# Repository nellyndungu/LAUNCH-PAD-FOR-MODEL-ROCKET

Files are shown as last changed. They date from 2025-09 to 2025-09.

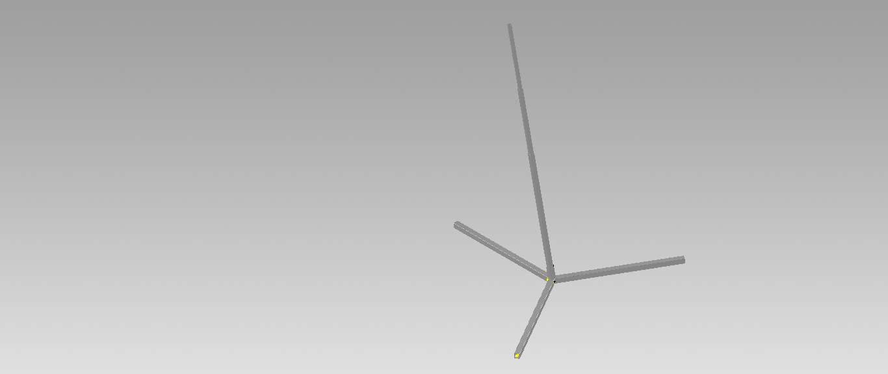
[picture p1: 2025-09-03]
LP001/LP.png

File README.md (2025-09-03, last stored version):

# LAUNCHPAD DESIGN
## DESIGN CONSIDERATION
1. Structural integrity.
The launchpad should withstand the forces/ thrust generated by the rocket during liftoff.
- Strong and rigid structural members – consider the material and the cross-sections and the suitable length.
- Stable base – consider the most stable base shape whether the square or triangle base.
- Assembly technique – consider single launch rail support or telescopic joining of the rail support.
- Fastening – Use of bolts. Consider the appropriate bolts to use.
2. Rocket alignment.
Use Open Rocket to find the vertical angle offset for optimum stability during lift off. Practical method of loading the rocket onto the launchpad.
- Easy rocket loading – release system for loading of rocket onto the launchpad.
3. Rocket launchpad height.
The launch rail required length of 5m. This requires launch support of 4m and an overhang of 1m.
4. Portability – Easy setup and portability.
- Telescopic assembly for launch rail support.
- Detachable base.
5. Fabrication.
The launchpad design should allow for fabrication using standard materials and locally available fabrication methods.
## Expected loading
1. Thrust generated by the rocket and weight of the rocket (Actual load)
2. Horizontal component of actual load – acts on the rail support beam.
## Design calculations
The mean thrust of the motor is 3kN. Using a safety factor of 2:
The design load is given by:
$ L_d = SF \times L_a $
where $L_d$ is design load, $SF$ is safety factor and $L_a$ is the actual load resulting to design load of 6 kN.
The horizontal component of the design load is given by:
$$ F_h = L_d \times sin \alpha $$
where $F_h$ is horizontal component of design load and \alpha is rocket tilt angle of 5° resulting to 523 N. The launch rail assumes a cantilever fixed at different point and made of hollow square tubes. The design load shall be used to calculate the base dimensions and base member sizing. The horizontal component force shall be used to size the rail support beams and their cross-section. The rail support is a cantilever beam with point load and fixed at base of the launchpad.

Taking:
- Length of beam (L) = 4 m = 4000 mm
- Point load (𝐹ℎ) = 523 N
- Material: Mild steel Yield strength (𝜎𝑦) = 250 MPa, E = 200 GPa
- Hollow square section:
$$ I = \frac{B^4 - (B - 2t) ^4}{12} $$
where $I$ is moment of inertia $B$ is the side of square tube in mm and $t$ is thickness of tube in mm.

    1. Maximum bending moment ($𝑀_{𝑚𝑎𝑥}$):
    $$ M_{max} = F_h \times L$$
    resulting to 2,092,000 Nmm
  2. Section modulus (S)
    $$ \sigma_{max} = \frac{|M_{max}| \cdot C}{I} \le \sigma_y $$
    Since:
       $$ S = \frac{I}{C} $$
           then
        $$ \sigma_{max} = \frac{|M_{max}|}{S} $$:
        $$ S = \frac{|M_{max}|}{\sigma_{max}} $$
  resulting to 8368 $mm^3$
  3. Cross-section dimensions $(B)$
  $$ I = \frac{B^4 - (B - 2t)^4}{12} $$
  Taking thickness of 3 mm:
  $$ S = \frac{B^4 - (B - 2t)^4}{12} $$
  resulting to 8368 $mm^3$
Expanding the equation using binomial expansion and solving for B as 50mm.
4. Check for maximum deflection.
Maximum deflection is given by:
$$ \delta = \frac{FL^3}{3EI} $$
The  moment of inertia I for the 70mm hollow square cross-section is given as:
$$ I = \frac{B^4 - (B - 2t)^4}{12} $$ resulting to 208,492 $mm^4$
The maximum deflection was found to be 268 mm. This deflection is huge and exceeds the maximum allowable deflection.

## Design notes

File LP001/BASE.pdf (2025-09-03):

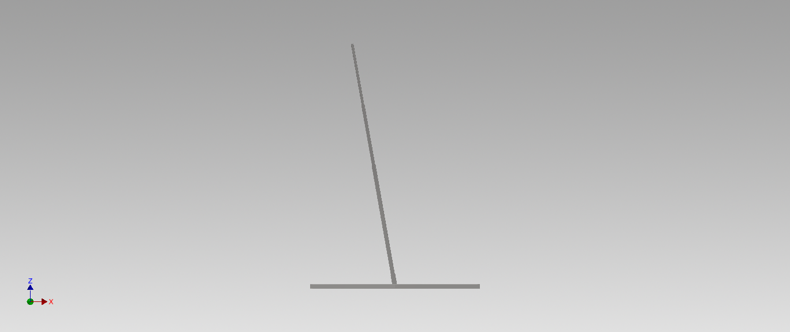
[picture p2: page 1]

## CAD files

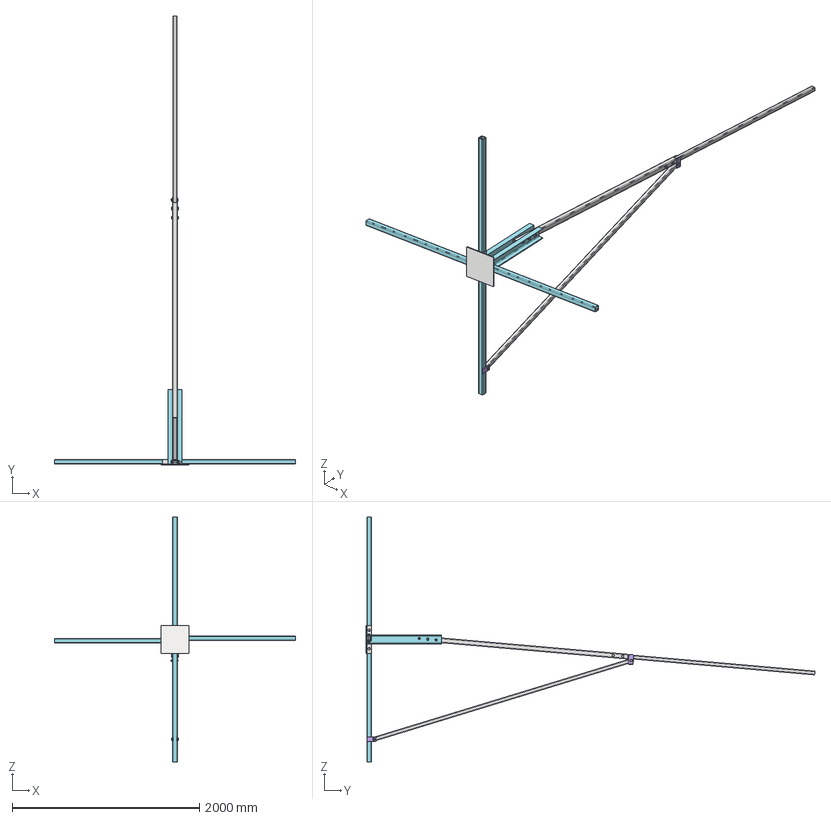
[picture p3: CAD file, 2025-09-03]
LP003/LPTL_ASSEMBLY.stp
2571.8 x 4791.2 x 2610.0 mm
BASE PLATE
U_SECTION x 2
Skeleton 1744276058427 x 2
ISO 657_11 CH 100 x 10 1744276061340
LEG_ATTACHMENT1
LEG_ATTACHMENT1_1
LEG_ATTACHMENT1_4 x 2
LEG x 4
Skeleton 1744274640470 x 4
ISO 12633-2 50x50x5 1744274642458 x 2
ANSI B18.2.3.5M - M16 x 2 x 80 x 5
ANSI B 18.2.4.1 M - M16 x 2 x 11
ISO 657_11 CH 100 x 10 1744276061340_1
LEG_ATTACHMENT1_2
LEG_ATTACHMENT1_3
ISO 12633-2 50x50x5 1744274642458_1
ISO 12633-2 50x50x5 1744274642458_2
ANSI B18.2.3.5M - M16 x 2 x 75 x 2
TL_FRAME x 2
Skeleton 1744350249536
ISO 10799-2 40x40x4 1744350251503
Skeleton 1744350148993
ISO 10799-2 50x50x4 1744350151616
ANSI B18.2.3.5M - M16 x 2 x 65 x 4
SUPPORT ATTACHMENT
SUPPORT ATTACHMENT_1
SUPPORT ATTACHMENT_2
SUPPORT ATTACHMENT_3
ENFORCEMENT_1
Skeleton 1744705197973
ISO 10799-2 40x40x4 1744708078713

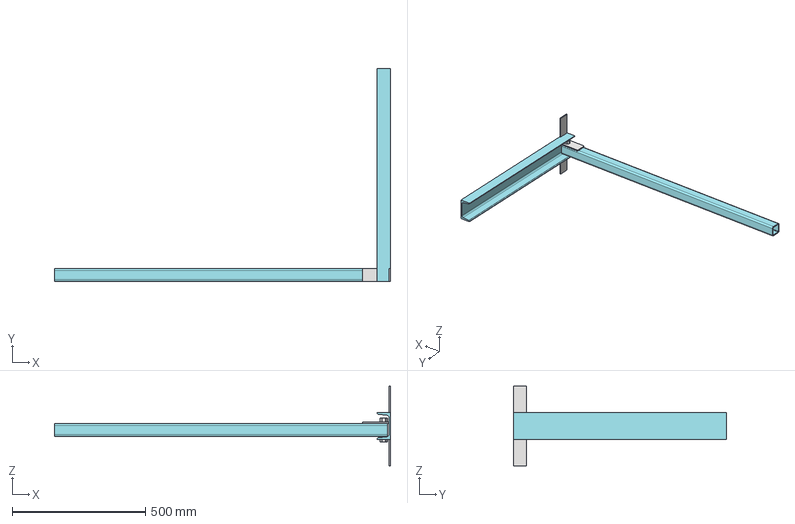
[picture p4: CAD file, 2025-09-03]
LP003/STEP_FILES/CHANNEL_LEG ASSEMBLY.stp
1260.9 x 800.0 x 300.0 mm
U_SECTION
Skeleton 1744276058427
ISO 657_11 CH 100 x 10 1744276061340
LEG_ATTACHMENT1 x 2
LEG_ATTACHMENT1_1
LEG
Skeleton 1744274640470
ISO 12633-2 50x50x5 1744274642458
ANSI B18.2.3.5M - M16 x 2 x 80
ANSI B 18.2.4.1 M - M16 x 2

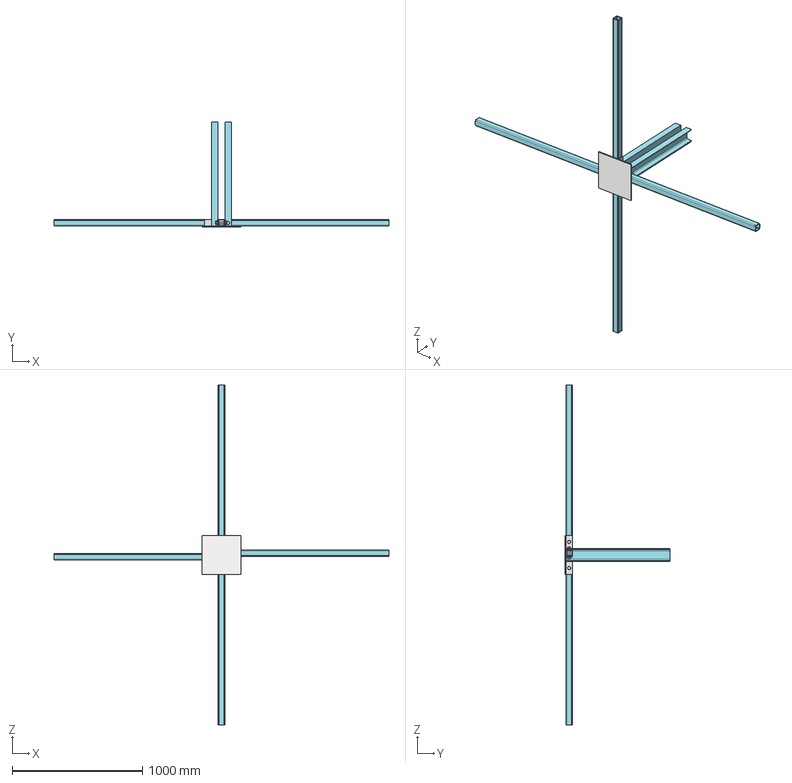
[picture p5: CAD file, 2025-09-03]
LP003/STEP_FILES/BASE_ASSEMBLY.stp
2571.8 x 808.0 x 2610.0 mm
BASE PLATE
U_SECTION x 2
Skeleton 1744276058427 x 2
ISO 657_11 CH 100 x 10 1744276061340 x 2
LEG_ATTACHMENT1
LEG_ATTACHMENT1_1
LEG_ATTACHMENT1_4 x 2
LEG x 4
Skeleton 1744274640470 x 4
ISO 12633-2 50x50x5 1744274642458 x 2
ANSI B18.2.3.5M - M16 x 2 x 80 x 2
ANSI B 18.2.4.1 M - M16 x 2 x 4
LEG_ATTACHMENT1_2
LEG_ATTACHMENT1_3
ISO 12633-2 50x50x5 1744274642458_1
ISO 12633-2 50x50x5 1744274642458_2
ANSI B18.2.3.5M - M16 x 2 x 75 x 2

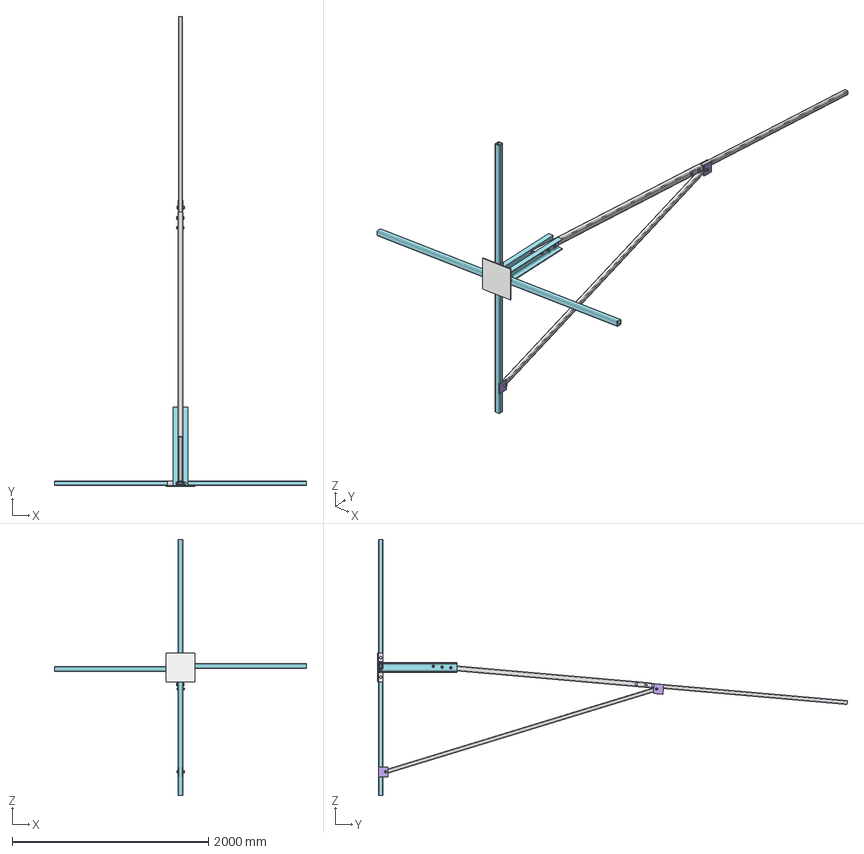
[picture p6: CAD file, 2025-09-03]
LP003/STEP_FILES/LPTL_ASSEMBLY WITH SUPPORT.stp
2571.8 x 4791.2 x 2610.0 mm
BASE PLATE
U_SECTION x 2
Skeleton 1744276058427 x 2
ISO 657_11 CH 100 x 10 1744276061340
LEG_ATTACHMENT1
LEG_ATTACHMENT1_1
LEG_ATTACHMENT1_4 x 2
LEG x 4
Skeleton 1744274640470 x 4
ISO 12633-2 50x50x5 1744274642458 x 2
ANSI B18.2.3.5M - M16 x 2 x 80 x 5
ANSI B 18.2.4.1 M - M16 x 2 x 11
ISO 657_11 CH 100 x 10 1744276061340_1
LEG_ATTACHMENT1_2
LEG_ATTACHMENT1_3
ISO 12633-2 50x50x5 1744274642458_1
ISO 12633-2 50x50x5 1744274642458_2
ANSI B18.2.3.5M - M16 x 2 x 75 x 2
TL_FRAME x 2
Skeleton 1744350249536
ISO 10799-2 40x40x4 1744350251503
Skeleton 1744350148993
ISO 10799-2 50x50x4 1744350151616
ANSI B18.2.3.5M - M16 x 2 x 65 x 4
SUPPORT ATTACHMENT
SUPPORT ATTACHMENT_1
ENFORCEMENT_1
Skeleton 1744705197973
ISO 10799-2 40x40x4 1744708078713
SUPPORT ATTACHMENT_2
SUPPORT ATTACHMENT_3

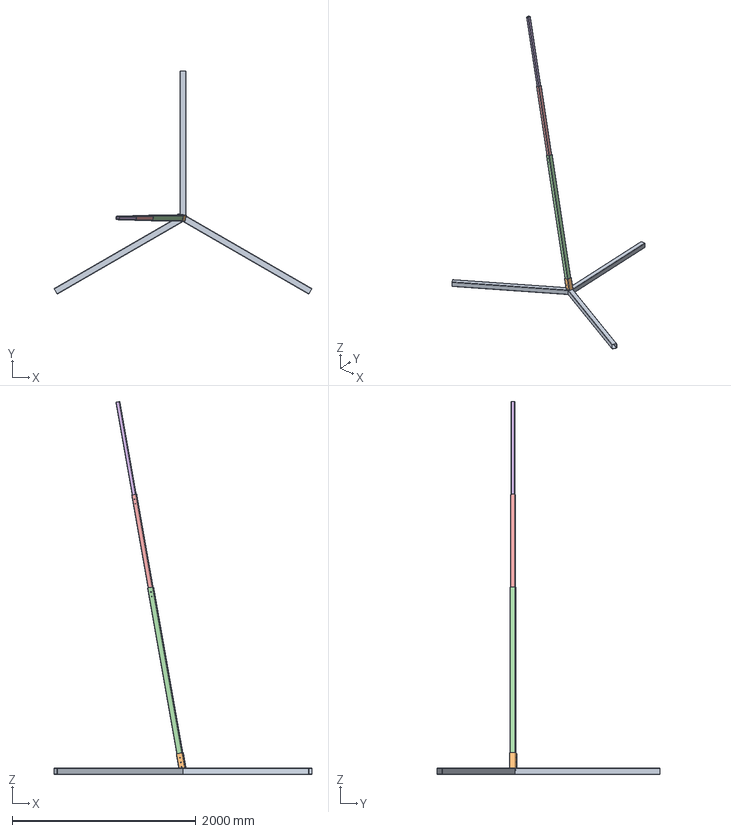
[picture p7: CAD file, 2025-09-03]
LP001/LAUNCHPAD.stp
2806.3 x 2430.3 x 4058.9 mm
BASE_1
Skeleton 1743054956772
ISO 10799-2 - 70x70x3 - 1600
ISO 10799-2 - 70x70x3 - 1600_1
ISO 10799-2 - 70x70x3 - 1600_2
ISO 10799-2 - 70x70x3 - 200
LP_01
Skeleton 1743052582824
ISO 10799-2 - 60x60x3 - 2000
LP_02 x 2
Skeleton 1743058174036
ISO 10799-2 - 50x50x3 - 1150
Skeleton 1743060041599
ISO 10799-2 - 40x40x3 - 1150

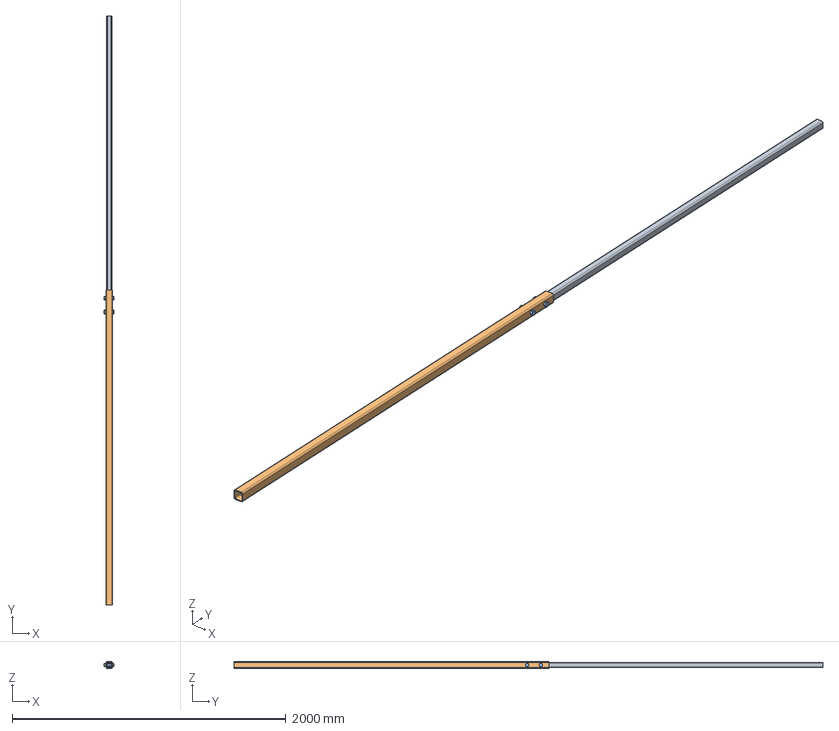
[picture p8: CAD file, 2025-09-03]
LP003/STEP_FILES/TL_50_40.stp
75.8 x 4300.0 x 50.0 mm
TL_FRAME x 2
Skeleton 1744350249536
ISO 10799-2 40x40x4 1744350251503
Skeleton 1744350148993
ISO 10799-2 50x50x4 1744350151616
ANSI B18.2.3.5M - M16 x 2 x 65 x 2
ANSI B 18.2.4.1 M - M16 x 2 x 2

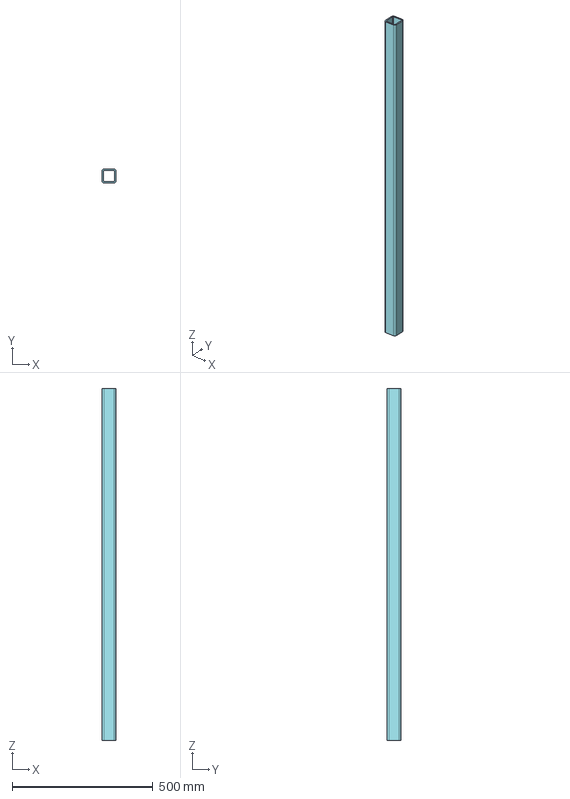
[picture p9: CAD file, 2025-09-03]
LP003/STEP_FILES/LEG_50.stp
50.0 x 50.0 x 1250.0 mm
LEG
Skeleton 1744274640470
ISO 12633-2 50x50x5 1744274642458

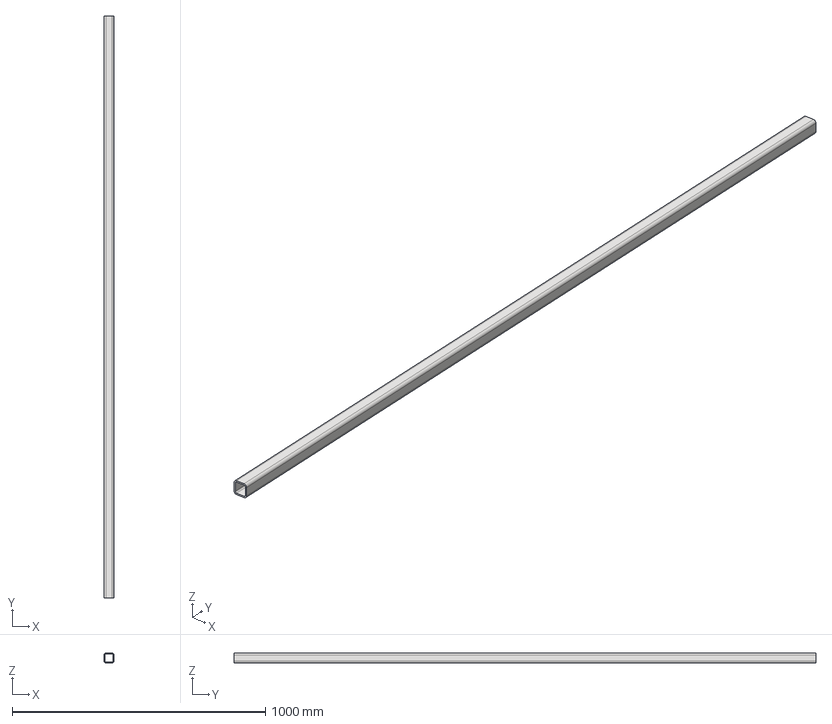
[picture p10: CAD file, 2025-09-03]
LP003/STEP_FILES/TL_40.stp
40.0 x 2300.0 x 40.0 mm
TL_FRAME
Skeleton 1744350249536
ISO 10799-2 40x40x4 1744350251503

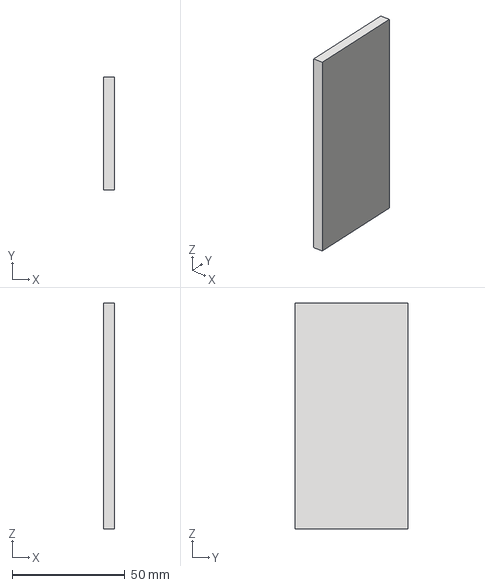
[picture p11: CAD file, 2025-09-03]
LP003/STEP_FILES/LEG_ATTACHMENT1.stp
5.00 x 50.0 x 100.0 mm

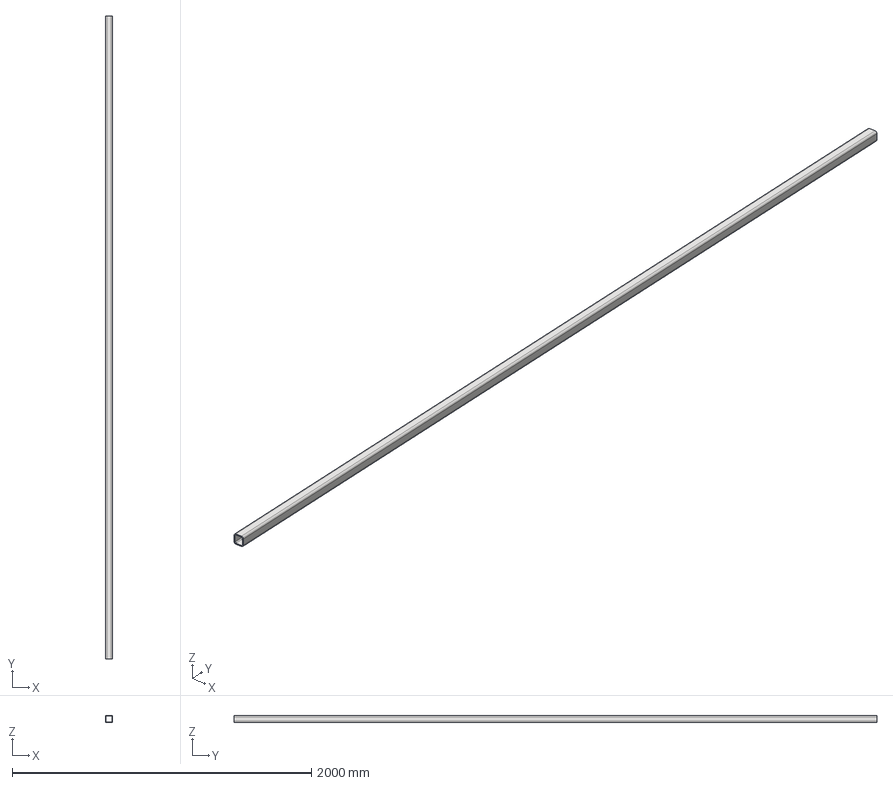
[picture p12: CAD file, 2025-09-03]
LP003/STEP_FILES/RAIL_SUPPORT_50.stp
50.0 x 4300.0 x 50.0 mm
RAIL_SUPPORT
Skeleton 1744280627170
ISO 10799-2 50x50x5 1744280629508

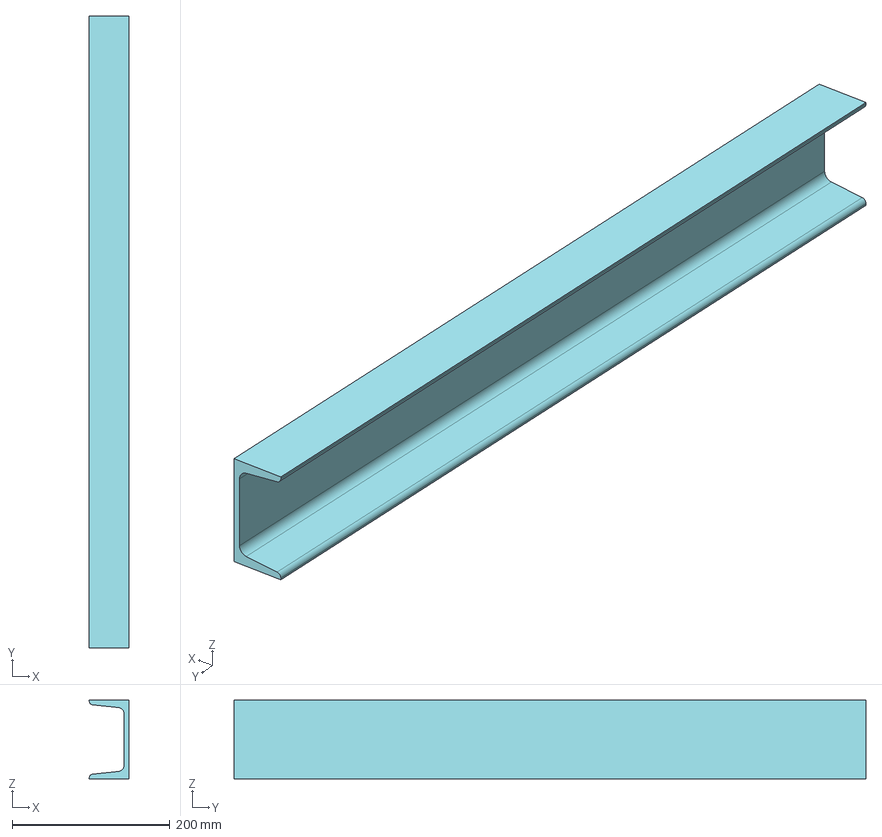
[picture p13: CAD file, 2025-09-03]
LP003/STEP_FILES/U_SECTION_50.stp
50.0 x 800.0 x 100.0 mm
U_SECTION
Skeleton 1744276058427
ISO 657_11 CH 100 x 10 1744276061340

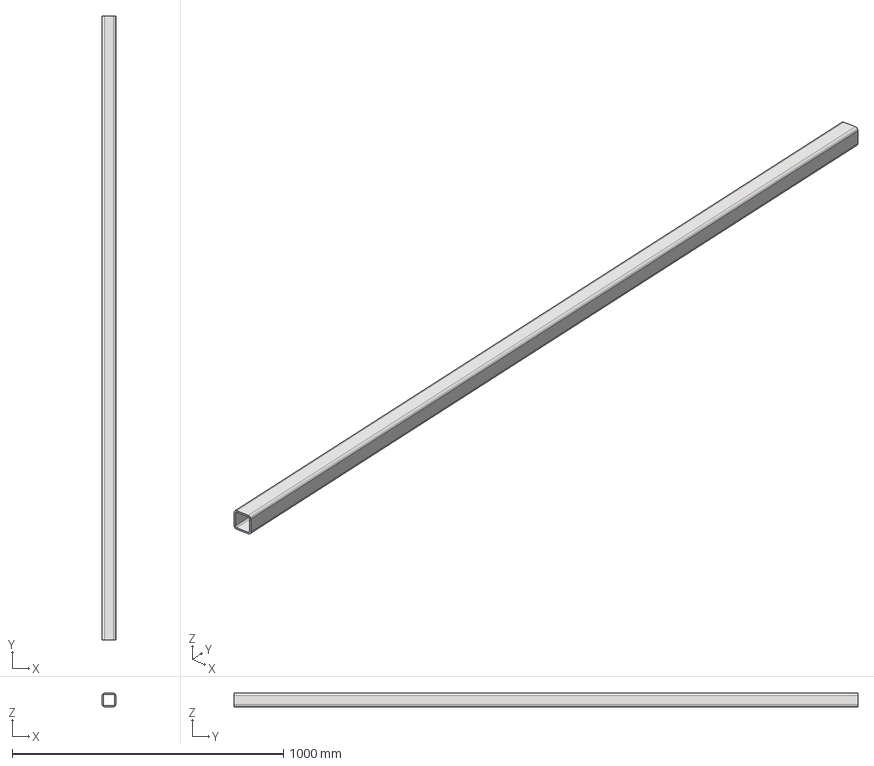
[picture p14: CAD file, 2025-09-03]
LP003/STEP_FILES/TL_50.stp
50.0 x 2300.0 x 50.0 mm
TL_FRAME
Skeleton 1744350148993
ISO 10799-2 50x50x4 1744350151616

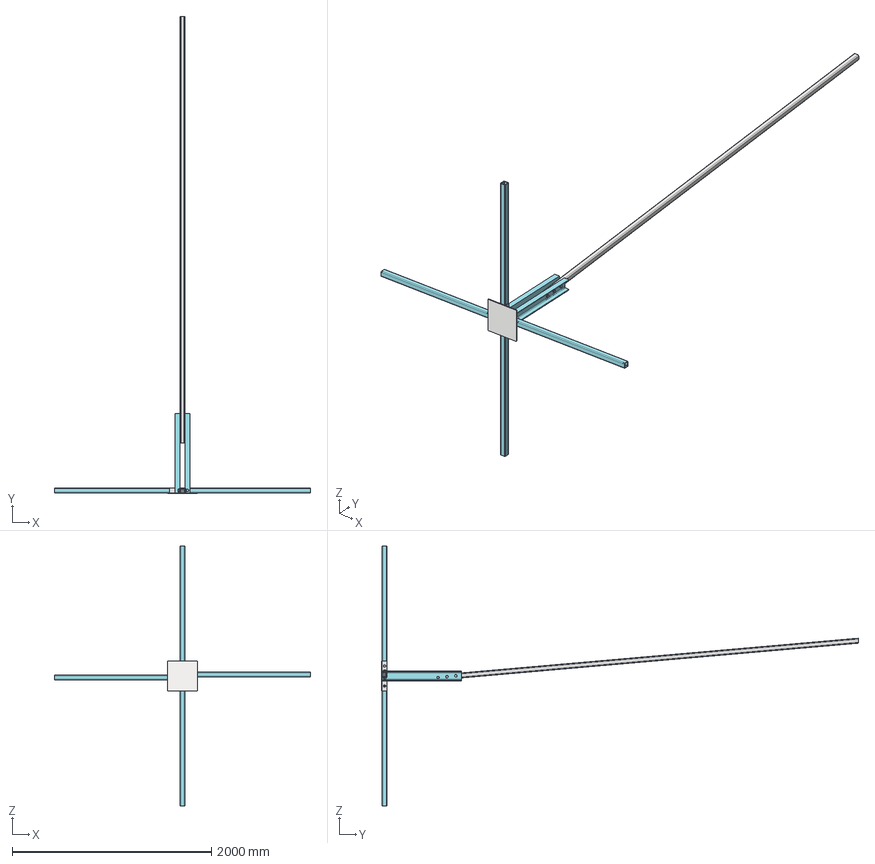
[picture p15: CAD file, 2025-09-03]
LP003/STEP_FILES/LP_003.stp
2571.8 x 4796.0 x 2610.0 mm
BASE PLATE
U_SECTION x 2
Skeleton 1744276058427 x 2
ISO 657_11 CH 100 x 10 1744276061340
LEG_ATTACHMENT1
LEG_ATTACHMENT1_1
LEG_ATTACHMENT1_4 x 2
LEG x 4
Skeleton 1744274640470 x 4
ISO 12633-2 50x50x5 1744274642458 x 2
ANSI B18.2.3.5M - M16 x 2 x 80 x 5
ANSI B 18.2.4.1 M - M16 x 2 x 7
ISO 657_11 CH 100 x 10 1744276061340_1
LEG_ATTACHMENT1_2
LEG_ATTACHMENT1_3
ISO 12633-2 50x50x5 1744274642458_1
ISO 12633-2 50x50x5 1744274642458_2
RAIL_SUPPORT
Skeleton 1744280627170
ISO 10799-2 50x50x5 1744280629508
ANSI B18.2.3.5M - M16 x 2 x 75 x 2

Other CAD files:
LP003/STEP_FILES/RAIL_SUPPORT.stp
LP003/STEP_FILES/U_SECTION.stp
LP003/STEP_FILES/TL_FRAME.stp
LP001/BASE.iam
LP001/BASE.ipn
LP001/BASE.ipt
LP001/BASE/Frame/Frame 1743053850590.iam
LP001/BASE/Frame/Frame 1743054956771.iam
LP001/BASE/Frame/ISO 10799-2 60x60x3 1743053853301.ipt
LP001/BASE/Frame/ISO 10799-2 60x60x3 1743053853449.ipt
LP001/BASE/Frame/ISO 10799-2 60x60x3 1743053853589.ipt
LP001/BASE/Frame/ISO 10799-2 70x70x3 1743054574629.ipt
LP001/BASE/Frame/ISO 10799-2 70x70x3 1743054959024.ipt
LP001/BASE/Frame/ISO 10799-2 70x70x3 1743054959175.ipt
LP001/BASE/Frame/ISO 10799-2 70x70x3 1743054959326.ipt
LP001/BASE/Frame/ISO 10799-2 70x70x3 1743054959485.ipt
LP001/BASE/Frame/ISO 10799-2 90x90x3 1743704209894.ipt
LP001/BASE/Frame/ISO 10799-2 90x90x3 1743704266901.ipt
LP001/BASE/Frame/ISO 10799-2 90x90x3 1743704267064.ipt
LP001/BASE/Frame/ISO 10799-2 90x90x3 1743704267227.ipt
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

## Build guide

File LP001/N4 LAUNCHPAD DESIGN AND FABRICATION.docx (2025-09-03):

# N4 LAUNCHPAD DESIGN AND FABRICATION

## DESIGN

Design considerations

1. Structural integrity – the launchpad should withstand the forces/ thrust generated by the rocket during liftoff.
  a. Requirements and options:
    i. Strong and rigid structural members – consider the material and the cross-sections and the suitable length.
    ii. Stable base – consider the most stable base shape whether the square or triangle base.
    iii. Assembly technique – consider single launch rail support or telescopic joining of the rail support.
    iv. Fastening – Use of bolts. Consider the appropriate bolts to use.
2. Rocket alignment – use Open Rocket to find the vertical angle offset for optimum stability during lift off. Practical method of loading the rocket onto the launchpad.
  a. Requirements and options
    i. Easy rocket loading – release system for loading of rocket onto the launchpad.
3. Rocket launchpad height – the launch rail required length of 5m. This requires launch support of 4m and an overhang of 1m.
4. Portability – Easy setup and portability.
  a. Requirements and options
    i. Telescopic assembly for launch rail support
    ii. Detachable base.
5. Fabrication – The launchpad design should allow for fabrication using standard materials and locally available fabrication methods.

## EXPECTED LOADING

1. Thrust generated by the rocket and weight of the rocket (Actual load)
2. Horizontal component of actual load – acts on the rail support beam.

## DESIGN CALCULATIONS

The mean thrust of the motor is 3kN. Using a safety factor of 2:

The design load is given by;

L_d =SF × L_a

where:

L_d is design load

SF is safety factor

La is actual load

resulting to design load of 6kN.

The horizontal component of the design load is given by

F_h =L_d ×sinα

where:

F_h is horizontal component of design load

α is rocket tilt angle of 5°

resulting to 523N.

The launch rail assumes a cantilever fixed at different point and made of hollow square tubes. The design load shall be used to calculate the base dimensions and base member sizing. The horizontal component force shall be used to size the rail support beams and their cross section.

The rail support is a cantilever beam with point load and fixed at base of the launchpad.

Taking:

- Length of beam (L) = 4 m = 4000 mm
- Point load ( F_h ) = 523 N
- Material: Mild steel Yield strength ( σ_y ) = 250 MPa, E = 200 GPa
- Hollow square section: I= (B^4 -(B-2t)^4)/12

Where:

    - I is moment of inertia
    - B is the side of square tube in mm
    - t is thickness of tube in mm
a) Maximum bending moment ( M_(max) )

M_(max) = F_h ×L=2,092,000 Nmm

b) Section modulus (S)

σ_(max) = (|M_(max) |c)/I ≤ σ_y

Since: S=I/C then σ_(max) = (|M_(max) |)/S :

S= (|M_(max) |)/(σ_(max)) = (2,092,000)/250 = 8368 mm³

c) Cross section dimensions (B)

I= (B^4 -(B-2t)^4)/12

Taking thickness as 3 mm:

S= (B^4 -(B-2t)^4)/12 = 8368 mm³

Expanding the equation using binomial expansion and solving for B as 50mm.

d) Check for maximum deflection

Maximum deflection is given by:

δ= (FL^3)/(3EI)

The moment of inertia I for the 70mm hollow square cross section is given as:

I= (B^4 -(B-2t)^4)/12

resulting to 208,492 mm⁴.

Substituting the values in the equation:

δ= (FL^3)/(3EI)

the maximum deflection was found to be 268 mm. This deflection is huge and exceeds the maximum allowable deflection.

## WAY FORWARD

Options to explore:

- Using a support reinforcement on one of the sides of the beam.
- Use truss instead of single telescopic bar.

## SIMULATIONS

The maximum displacement is 47.9252 mm, which could impact structural integrity.

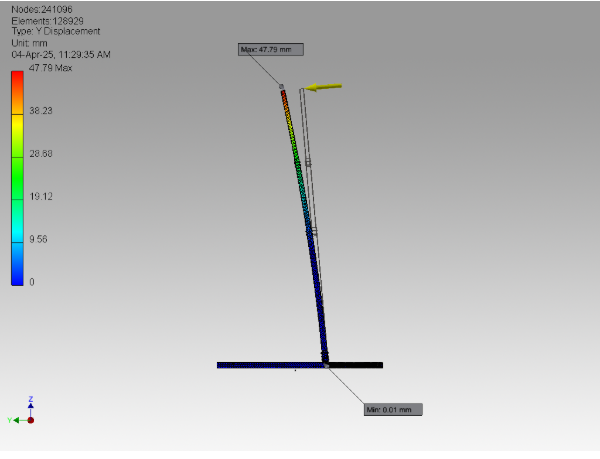
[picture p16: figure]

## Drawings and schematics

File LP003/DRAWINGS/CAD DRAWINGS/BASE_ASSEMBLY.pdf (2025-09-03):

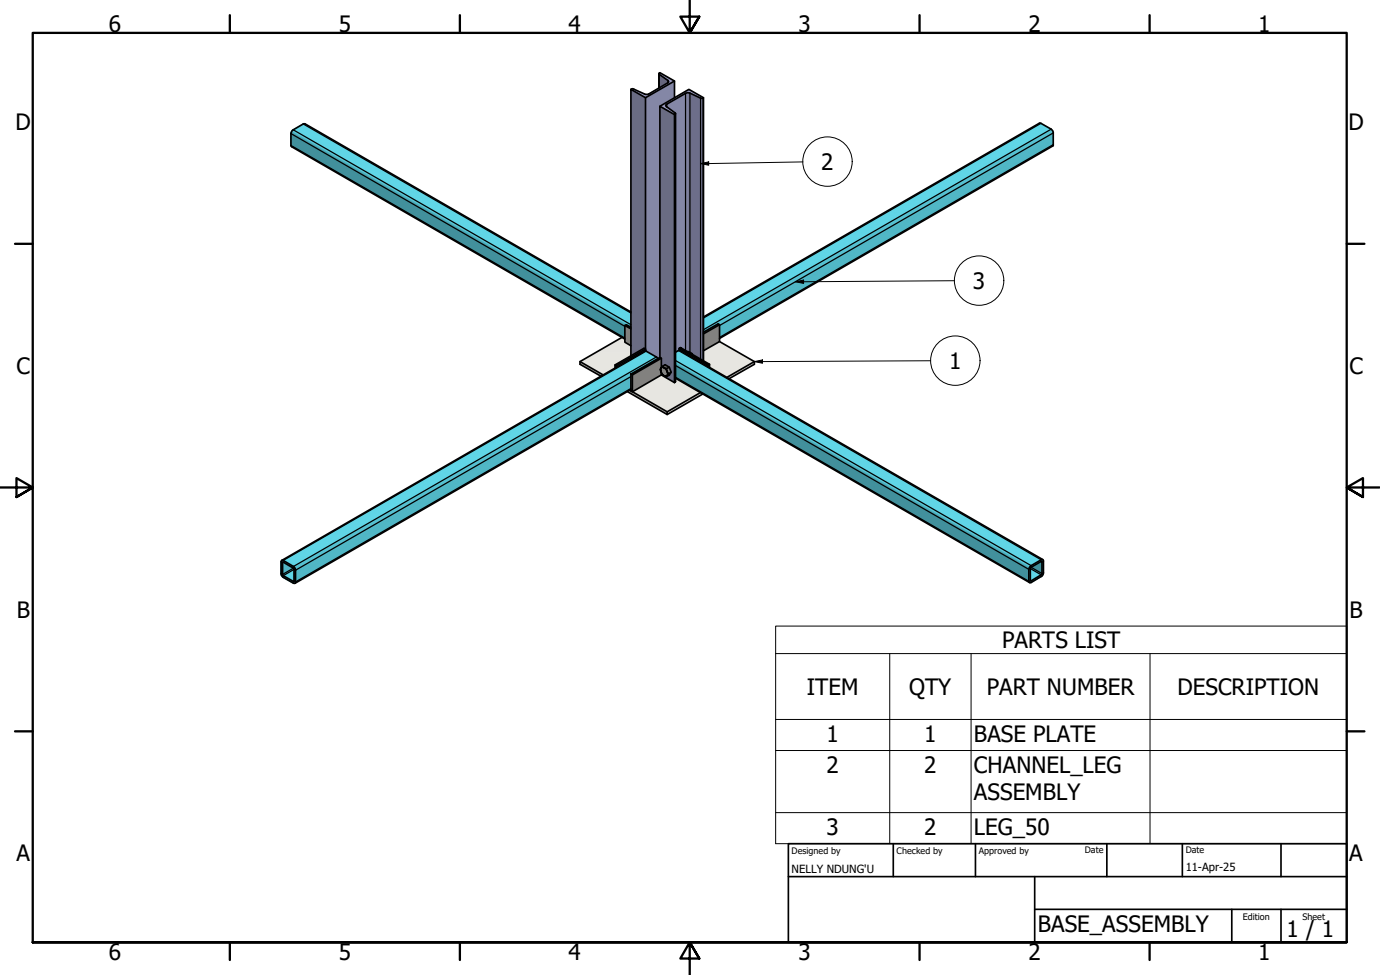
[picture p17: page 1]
PARTS LIST

ITEM | QTY | PART NUMBER | DESCRIPTION

1 | 1 | BASE PLATE
2 | 2 | CHANNEL_LEG ASSEMBLY

3 | 2 | LEG_50

Designed by NELLY NDUNG'U | Checked by | Approved by Date | | Date 11-Apr-25

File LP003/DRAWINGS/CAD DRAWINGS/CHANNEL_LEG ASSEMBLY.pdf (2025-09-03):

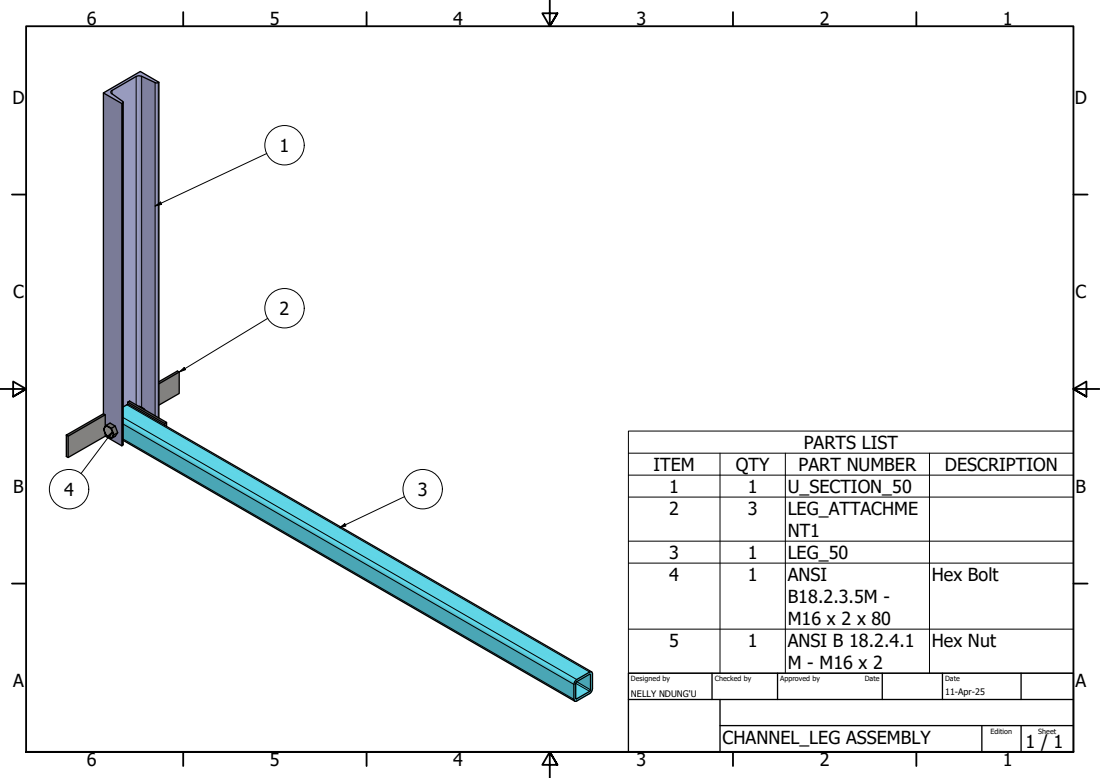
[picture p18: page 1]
PARTS LIST; CHANNEL_LEG ASSEMBLY

ITEM | QTY | PART NUMBER | DESCRIPTION
1 | 1 | U_SECTION_50
2 | 3 | LEG_ATTACHME NT1

3 | 1 | LEG_50
4 | 1 | ANSI B18.2.3.5M -M16 x 2 x 80 | Hex Bolt

5 | 1 | ANSI B 18.2.4.1 M - M16 x 2 | Hex Nut

Designed by NELLY NDUNG'U | Checked by | Approved by Date | | Date 11-Apr-25

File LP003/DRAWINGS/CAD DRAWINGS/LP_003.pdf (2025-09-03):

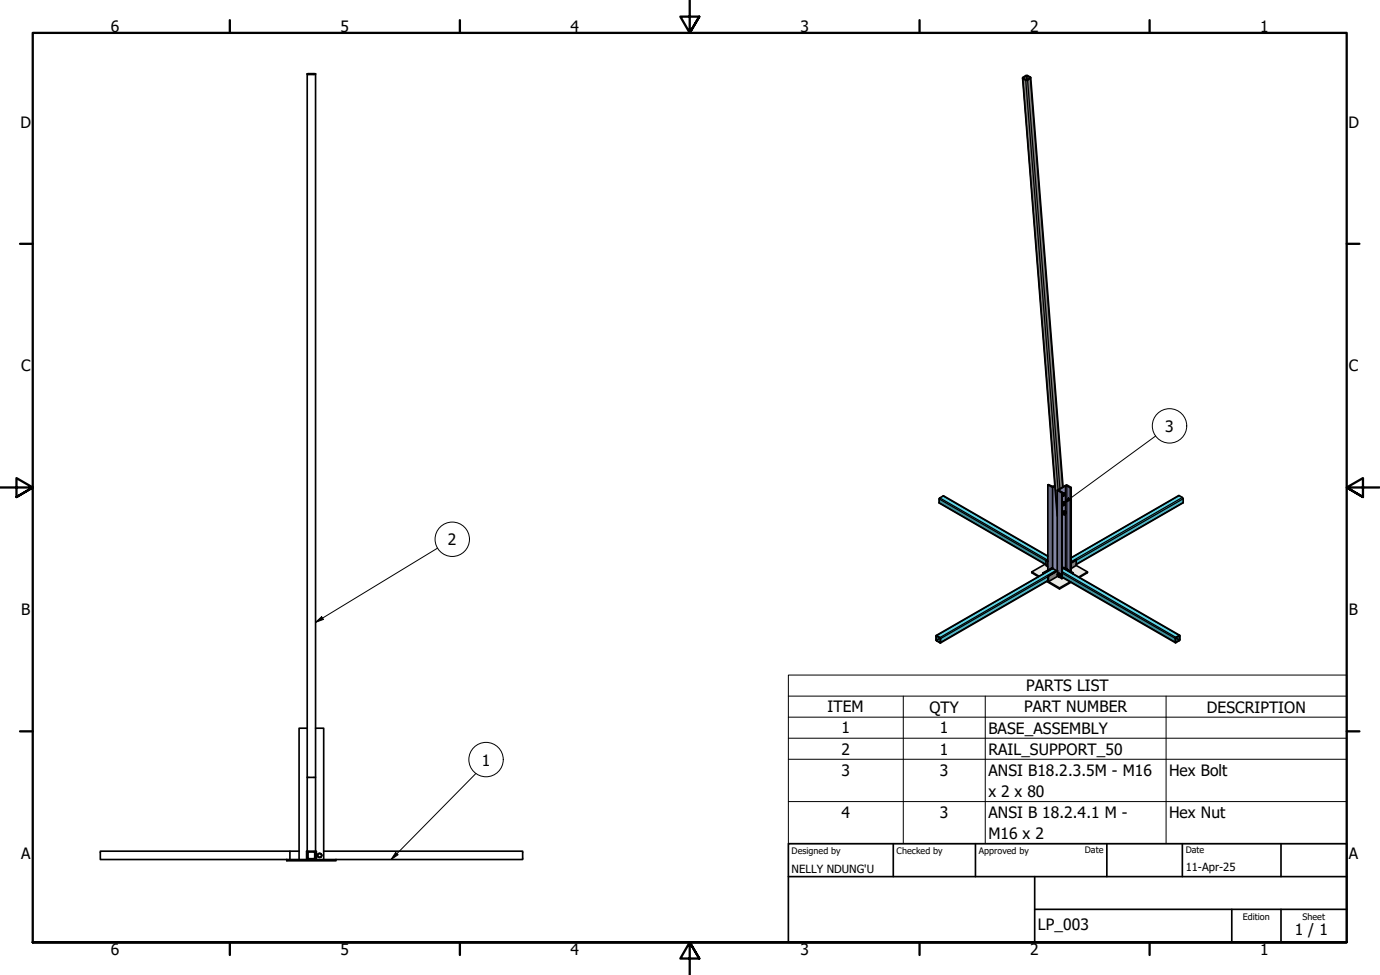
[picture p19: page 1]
PARTS LIST

ITEM | QTY | PART NUMBER | DESCRIPTION
1 | 1 | BASE_ASSEMBLY
2 | 1 | RAIL_SUPPORT_50
3 | 3 | ANSI B18.2.3.5M - M16 x 2 x 80 | Hex Bolt

4 | 3 | ANSI B 18.2.4.1 M -M16 x 2 | Hex Nut

Designed by NELLY NDUNG'U | Checked by | Approved by Date | | Date 11-Apr-25

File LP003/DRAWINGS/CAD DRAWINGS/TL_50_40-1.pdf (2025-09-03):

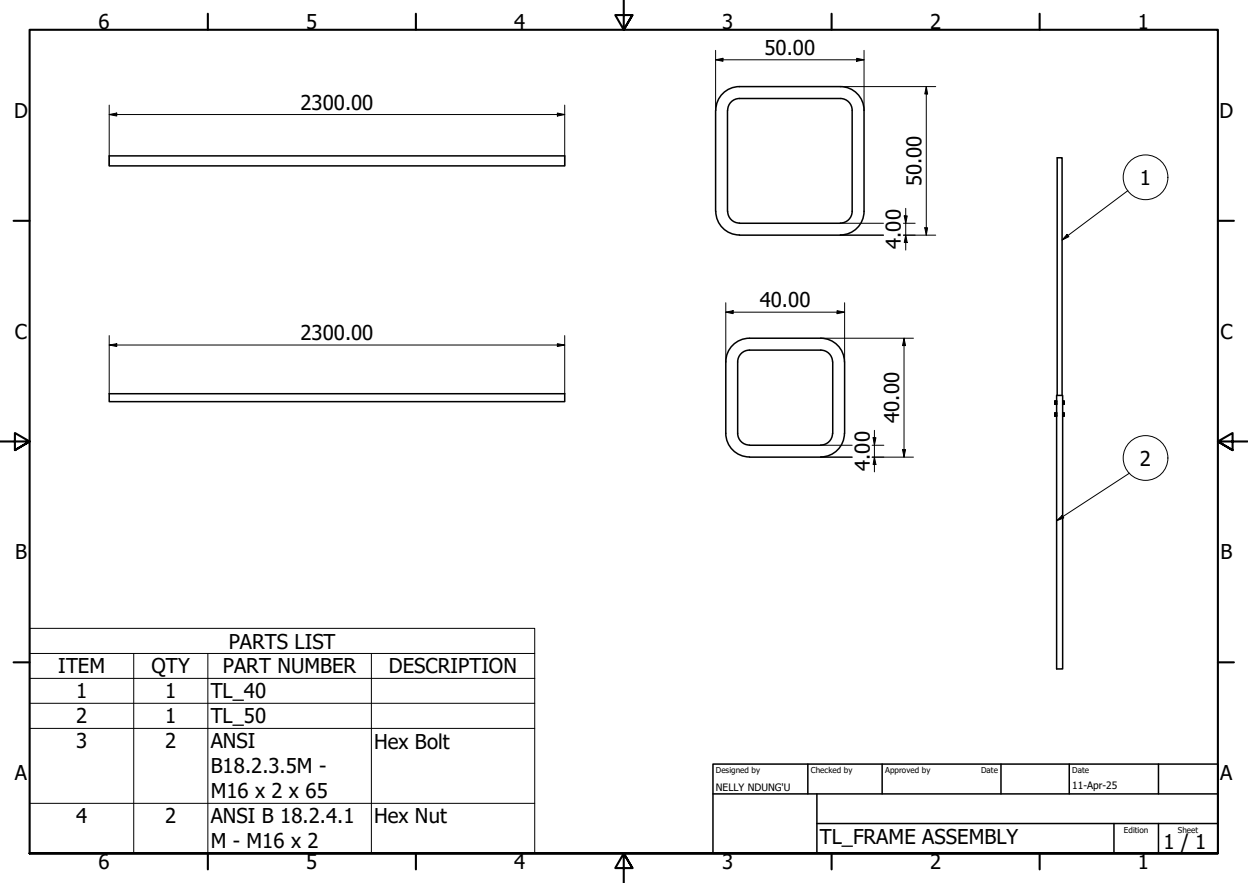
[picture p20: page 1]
PARTS LIST; NELLY NDUNG'U; 11-Apr-25; Designed by; Checked by; Approved by; Date

ITEM | QTY | PART NUMBER | DESCRIPTION
1 | 1 | TL_40
2 | 1 | TL_50
3 | 2 | ANSI B18.2.3.5M -M16 x 2 x 65 | Hex Bolt

4 | 2 | ANSI B 18.2.4.1 M - M16 x 2 | Hex Nut

TL_FRAME ASSEMBLY | Edition | Sheet 1 / 1

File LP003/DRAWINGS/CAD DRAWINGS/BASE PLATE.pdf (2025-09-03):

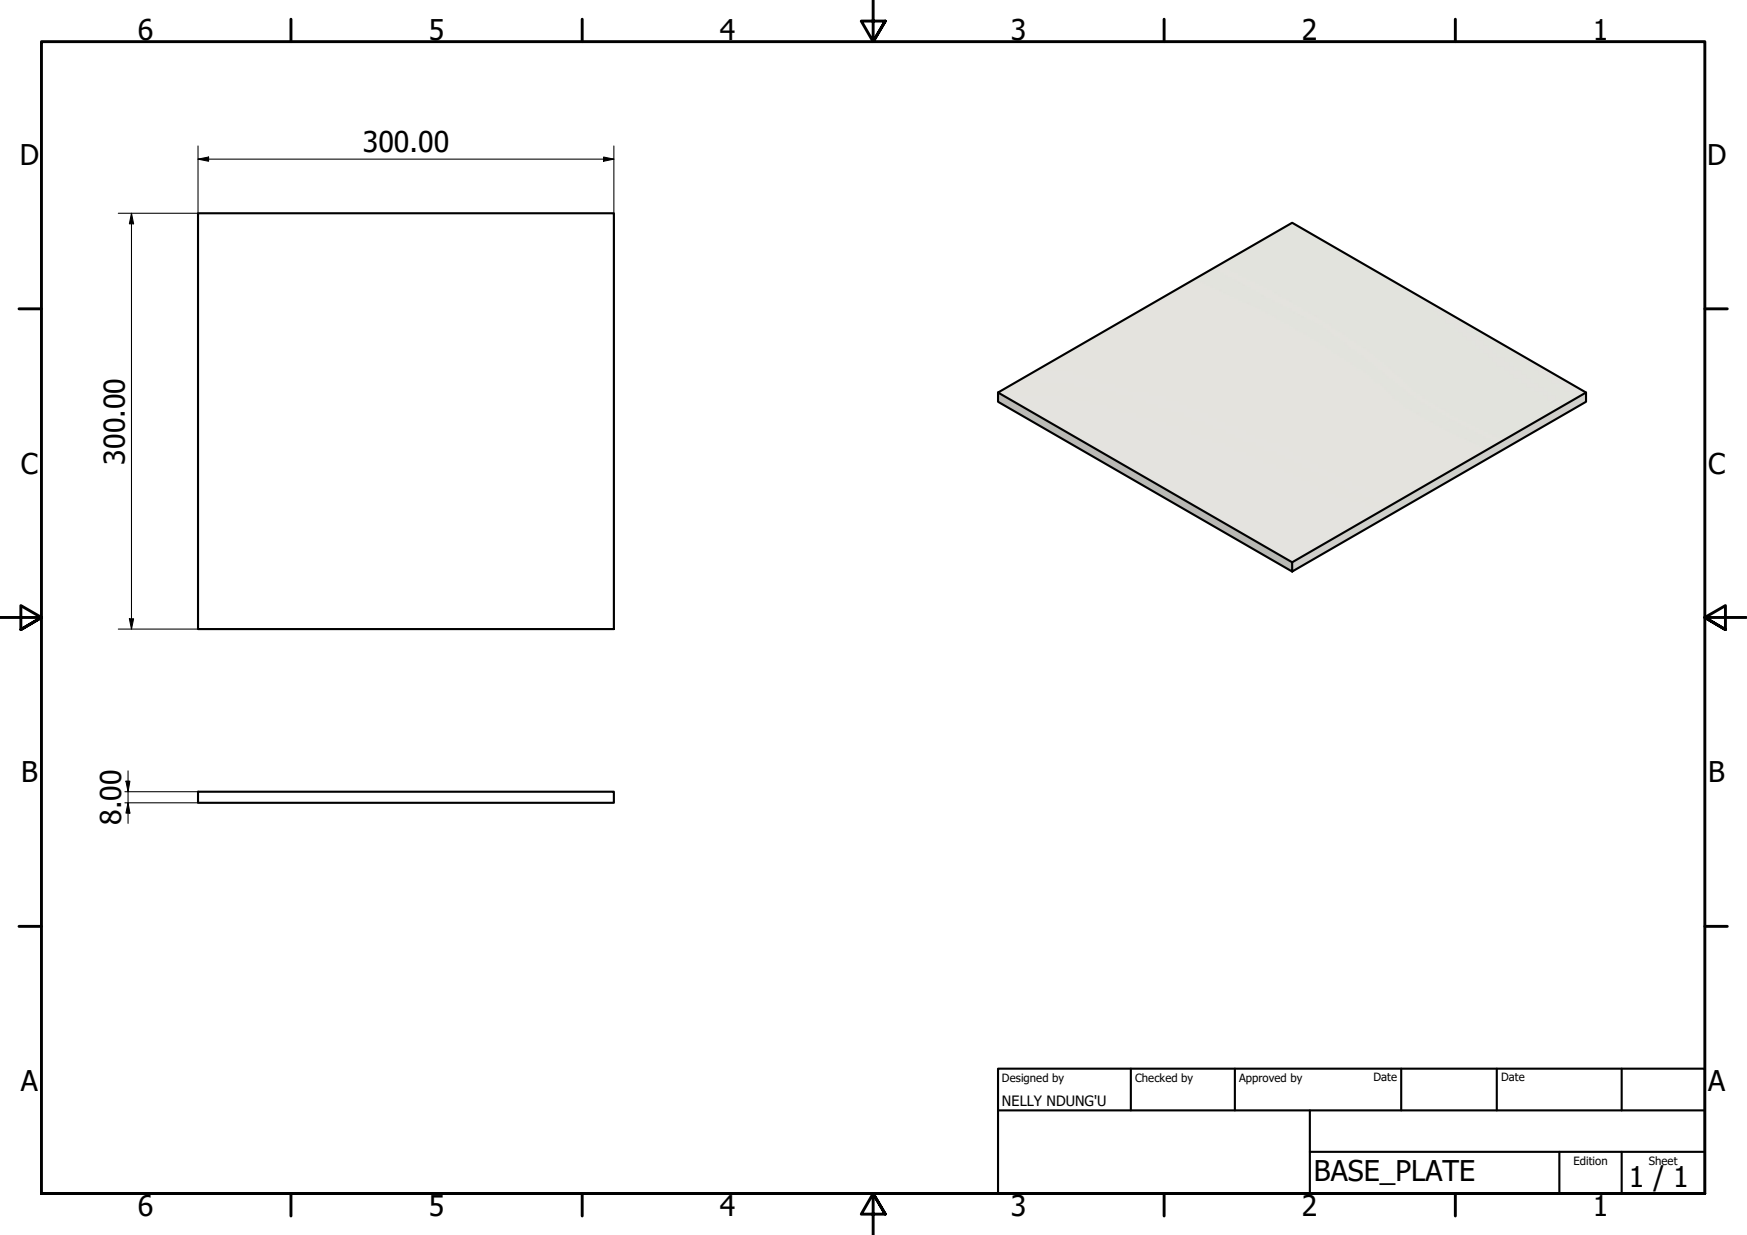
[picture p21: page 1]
NELLY NDUNG'U; Designed by; Checked by; Approved by; Date

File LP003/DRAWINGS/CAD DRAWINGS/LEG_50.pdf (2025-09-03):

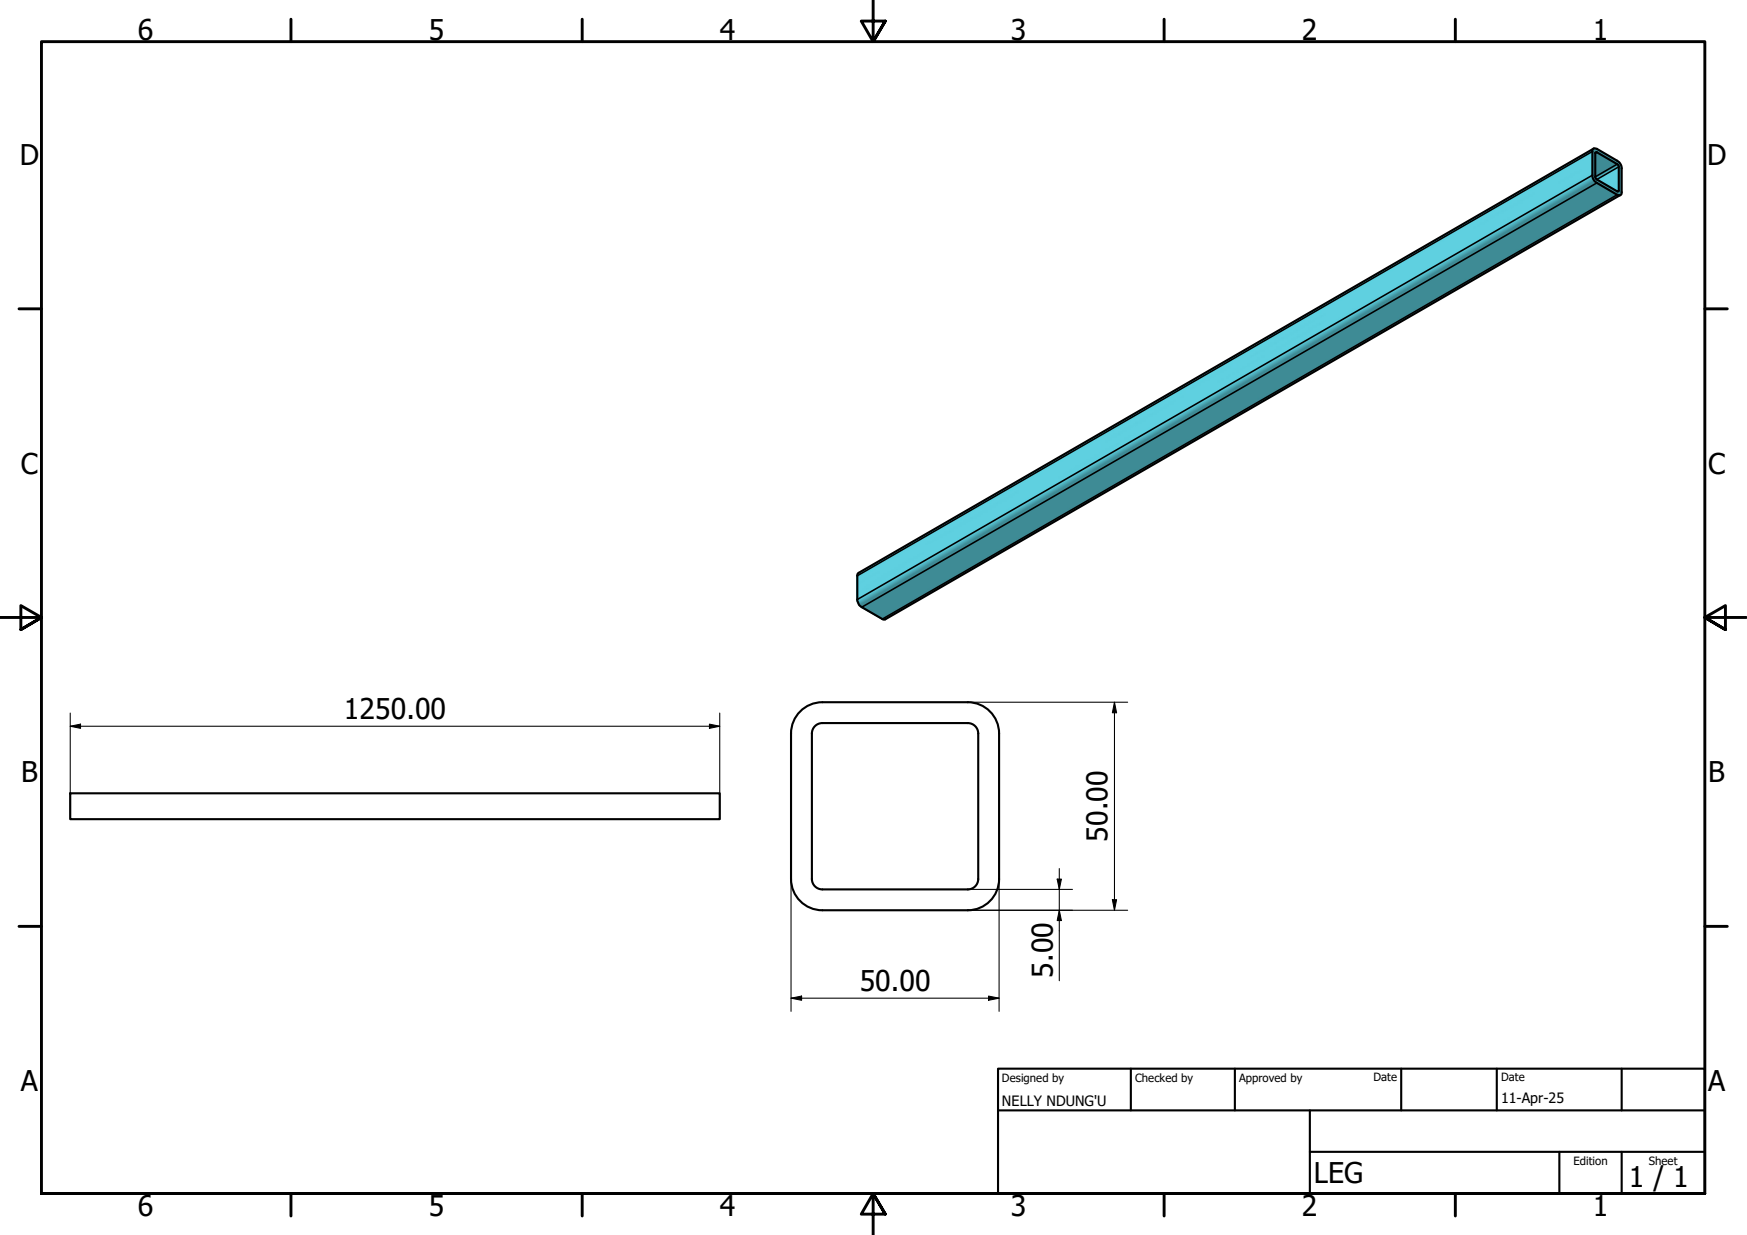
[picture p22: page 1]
NELLY NDUNG'U; 11-Apr-25; Designed by; Checked by; Approved by; Date

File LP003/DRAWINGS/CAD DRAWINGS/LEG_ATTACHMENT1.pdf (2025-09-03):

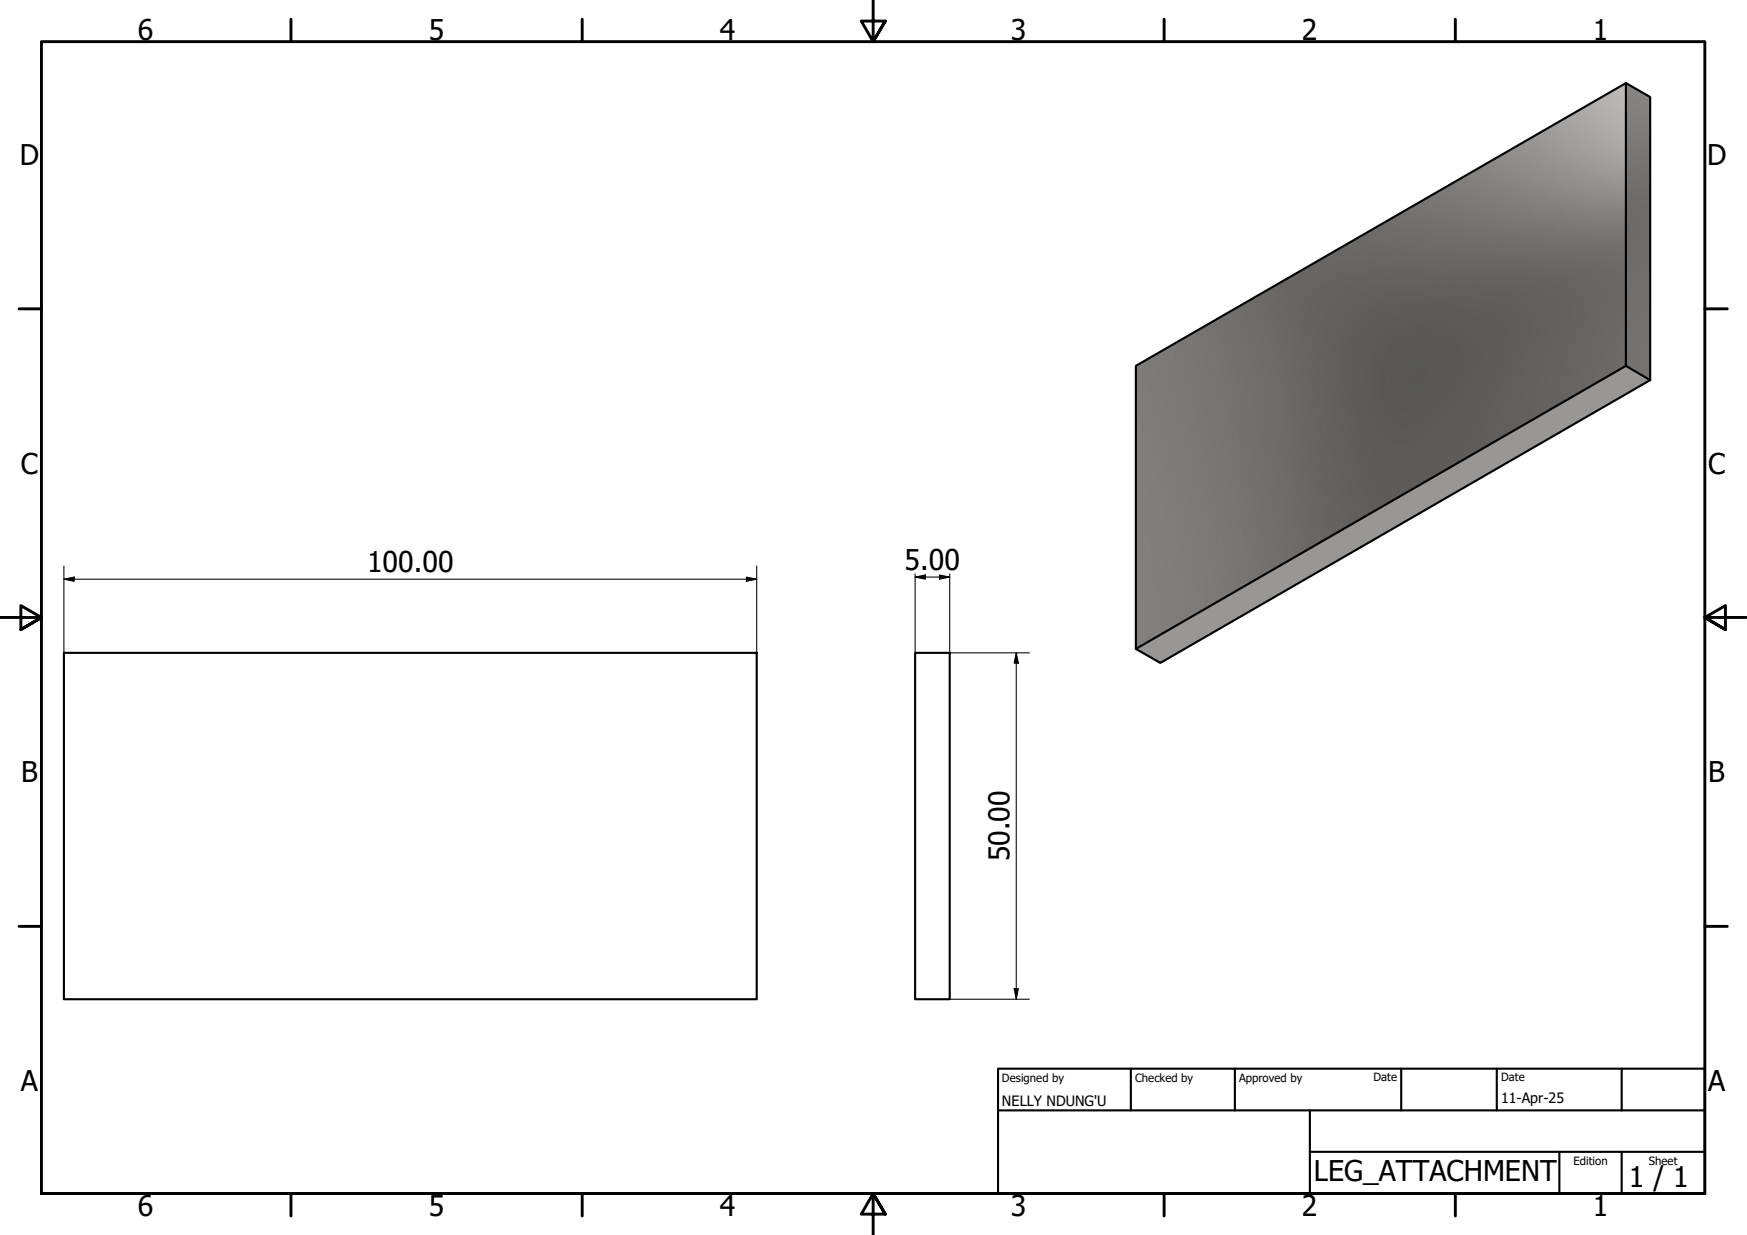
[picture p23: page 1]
NELLY NDUNG'U; 11-Apr-25; Designed by; Checked by; Approved by; Date

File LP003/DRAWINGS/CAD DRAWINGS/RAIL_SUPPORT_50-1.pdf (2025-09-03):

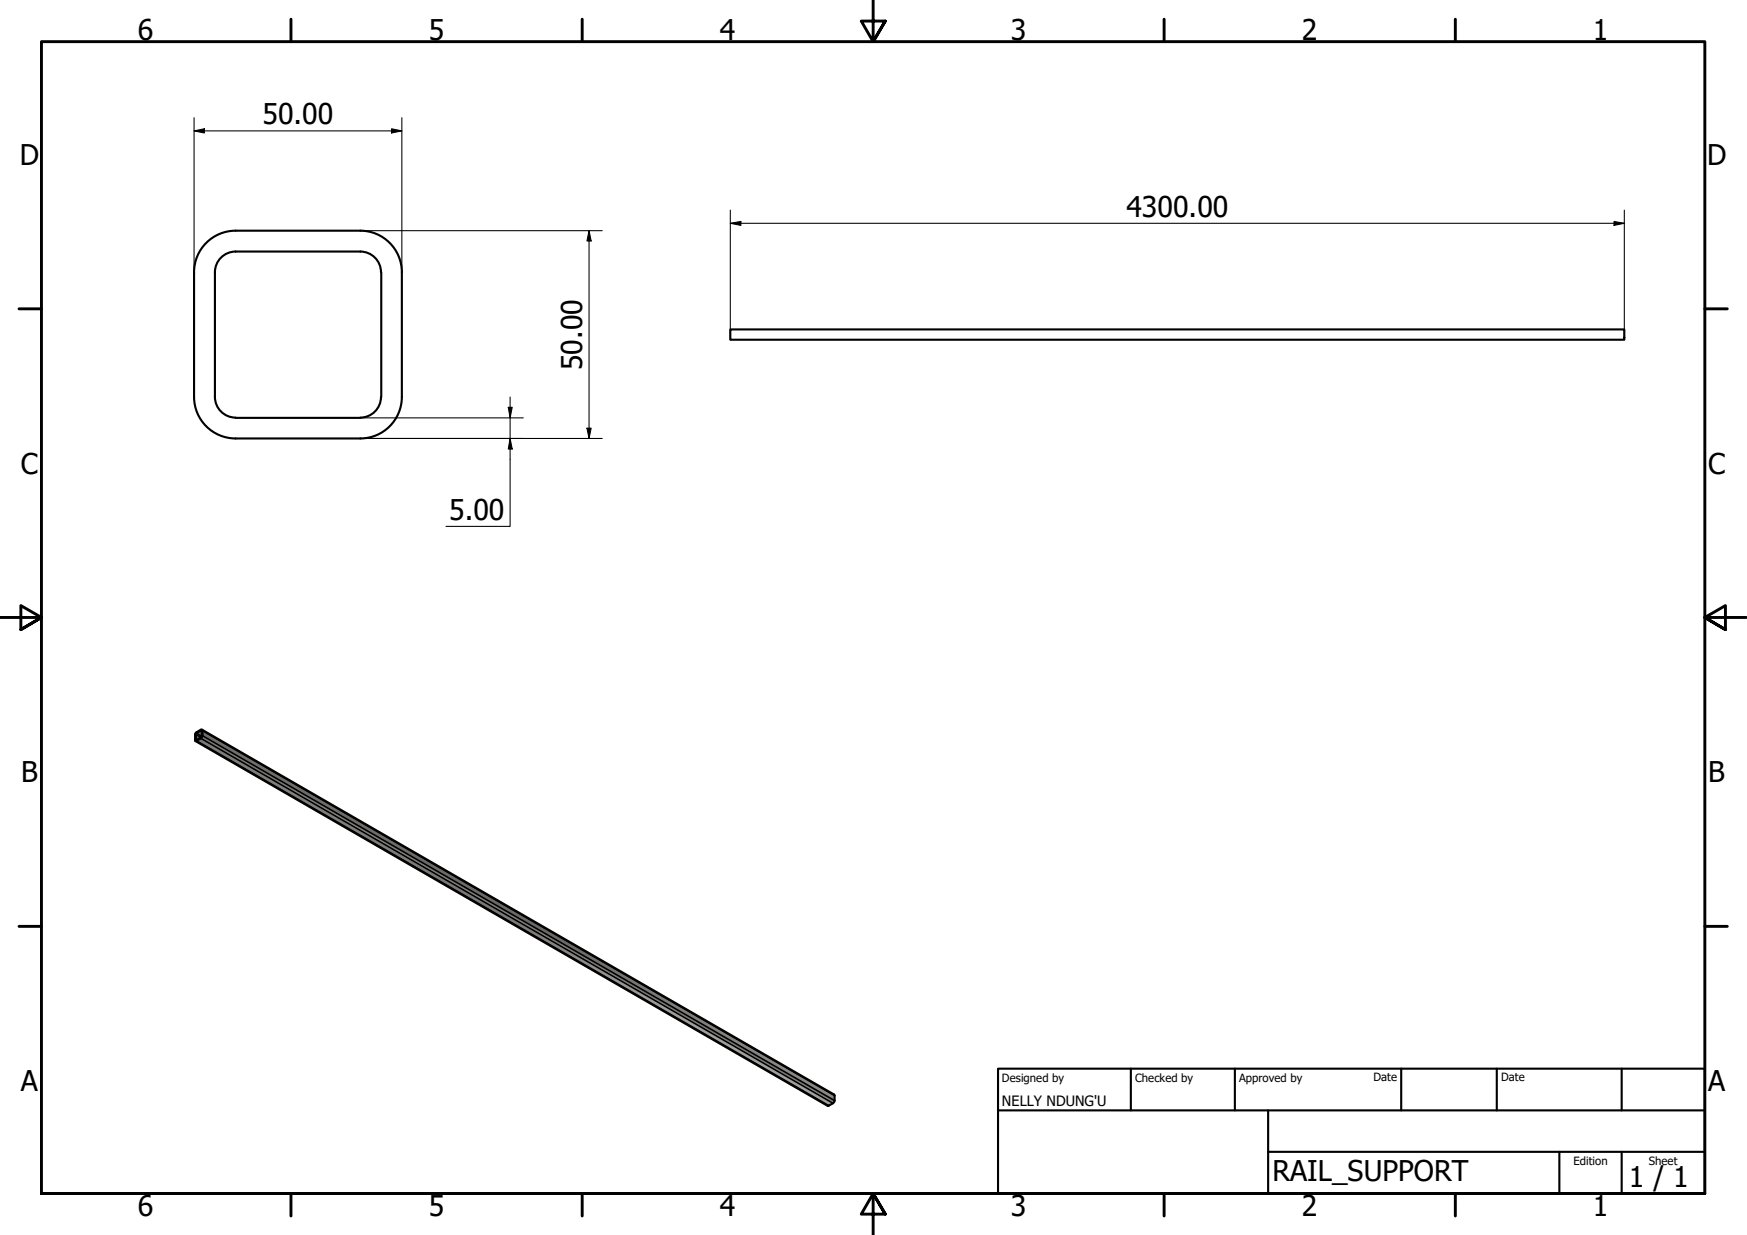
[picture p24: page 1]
NELLY NDUNG'U; Designed by; Checked by; Approved by; Date

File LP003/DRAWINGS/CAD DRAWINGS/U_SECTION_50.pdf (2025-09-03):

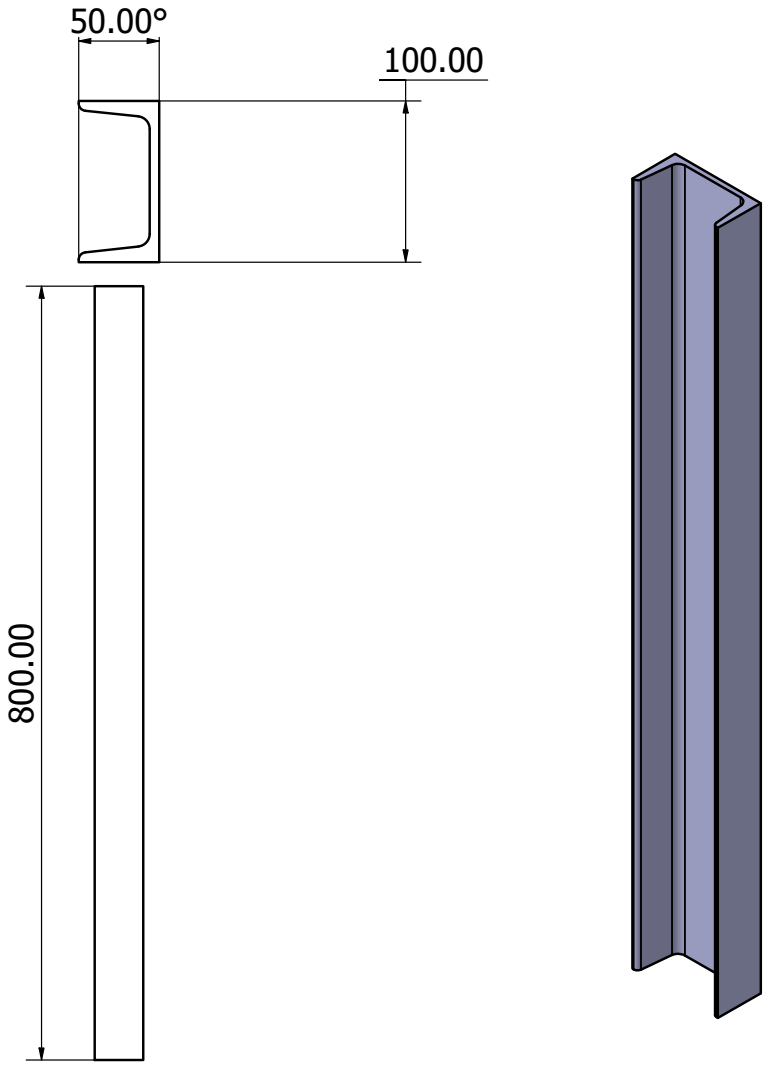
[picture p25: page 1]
NELLY NDUNG'U; Designed by; Checked by; Approved by; Date

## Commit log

2025-09-03 Initial version
    [BASE.0005.iam, BASE.0008.ipt, BASE.iam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]
2025-09-03 Second Launchpad version
    [BASE PLATE.ipt, BASE_002.0004.iam, BASE_002.iam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]
2025-09-03 Third version of launchpad
    [BASE PLATE.0001.ipt, BASE PLATE.idw, BASE PLATE.ipt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]
